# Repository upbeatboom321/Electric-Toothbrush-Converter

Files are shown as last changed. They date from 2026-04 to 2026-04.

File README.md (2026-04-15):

# Electric-Toothbrush-Converter

## Project Overview:

This project explores the design of a compact motor driven mechanism that converts a standard manual toothbrush into a high frequency electric toothbrush.

The goal is to design a mechanically efficient system that either: 1) produces strong, controlled vibration at the brush head or 2) a oscillating mechanism that moves that causes the brush to move with high frequency. All while remaining compact, handheld, battery powered, and modular.

## Problem Statement

Commercial electric toothbrushes are often expensive and proprietary. This project investigates whether a removable insert style handle can convert a standard manual toothbrush into a high frequency vibrating toothbrush using a compact DC motor system.

The challenge is efficiently transmitting vibration from the motor to the brush head without excessive damping or energy loss.

## Design Requirements

- Target vibration speed: 8000-20000RPM
- Power source: 3xAAA batteries in series
- Compact handheld form factor
- Replaceable manual toothbrush compatibility
- Safe and comfortable vibration amplitude

## Concept Selection

Two vibration approaches were considered.

Eccentric rotating mass motor/ vibration motor
A DC motor with an off center mass that generates vibration through centrifugal force.

Crank driven oscillation
A DC motor driving a crank mechanism that converts rotational motion into controlled angular oscillation.

Selected approach: The approach chosen for this project will involve a vibration motor. 

Rationale: A vibration motor was chosen over a crank driven oscillation mechanism because it is mechanically simpler, more compact, and easier to prototype. The vibration motor can generate high frequency motion with fewer moving parts, which reduces design complexity, manufacturing difficulty, and the risk of mechanical failure. This makes it more suitable for an early stage prototype where the main goal is to achieve noticeable brush vibration quickly and reliably.

## How the Mechanism Works

The vibration motor is mounted at the end of a link bar while the Toothbrush is clipped at the other end which allows to transfer vibration across.

## Mechanical Design

The mechanical system consists of:

- A Vibration motor
- A link bar
- A toothbrush clip
- A housing to support and align the mechanism

The mechanism is intended to be 3D printed for rapid prototyping and testing.

### Current Design Notes

- Motion type: Vibration motor
- Estimated motor vibration with brush: 8000-20000RPM
- Material: PLA plastic
- Mounting method: Press fit

---

## Electronics

### Planned Components

- Battery: 3xAAA batteries in series (4.5v)
- Switch: On off switch
- Motor control: direct power

### Electrical Goals

- Maintain stable motor speed under load
- Keep power system compact
- Avoid overheating
- Allow repeatable testing

---

## CAD and Prototyping

This project will use CAD and 3D printing to develop the mechanism and housing.

### Design Focus

- Lightweight moving parts
- Low backlash in the linkage
- Rigid motor mounting
- Compact toothbrush attachment system
- Easy disassembly for testing and iteration

---
# Current
---

## Current Specifications and Version

**Configuration:**  
- Motor: DC Coreless Vibration Motor 7x25mm, 1-6V Rated, 8000-20000RPM
- Power source: 3xAAA batteries in series
- Material: PLA plastic
- Brush attachment: Semi-cicrle like clip that goes around the lower midpoint of the brush

Current: Version 4
---

## Electrical Diagram

The electric wiring for this project is quite simple represented by the following diagram.

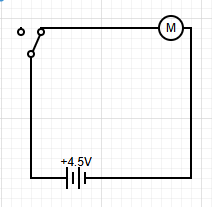
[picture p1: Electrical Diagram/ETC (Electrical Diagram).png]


Inside the acutal Main body of the ETC, where the battery positive and negative terminal make contact with the plastic, small pieced of metal were placed there connected to wires. This allows for the battery to be replacable while ensuring proper connection.

## Future corrections

The ETC is effective and there is substancial vibration at the brush head, however the vibration mechanism is making too much noise. The link bar making contact with the surrounding enviroment is causing the vibration to transfer to the whole body and not just the brush head. The vibration motor is further dampened by the switch located in side the main body due to it being to big and making direct contact with the motor. The case is okay but becomes uncomfortable to hold when brushing the top teeth. The brush also turns while brushing causing there to be less overall vibration.

Too make is product more effective: the material surrounding the link bar will need to make less contact while not degrading structual integrety, the switch will need to be smaller to give more room for the vibration motor, the casing will need to be more confortable to hold using ergonomic designs, the clip for the brush needs to be universal while firmly holding onto the any brush.

## Final Photos

![image alt]([https://github.com/upbeatboom321/Electric-Toothbrush-Converter/blob/edd6b2010d671f4ffcdd68ea69ed5afbbf082775/Electrical%20Diagram/ETC%20(Electrical%20Diagram).png](https://github.com/upbeatboom321/Electric-Toothbrush-Converter/blob/bc1a8993c03731aabfaebd6da449c6d216bca477/ETC%20Media/ETC%20(Final%20with%20everything).jpeg))

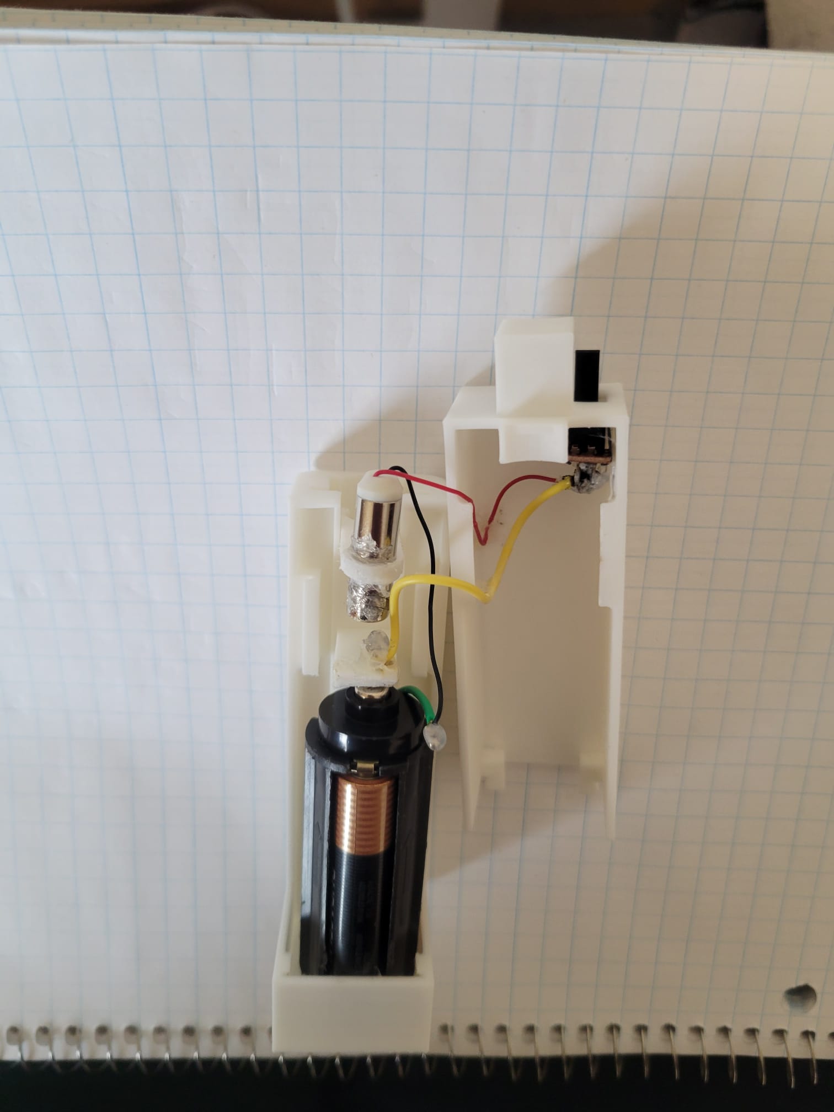
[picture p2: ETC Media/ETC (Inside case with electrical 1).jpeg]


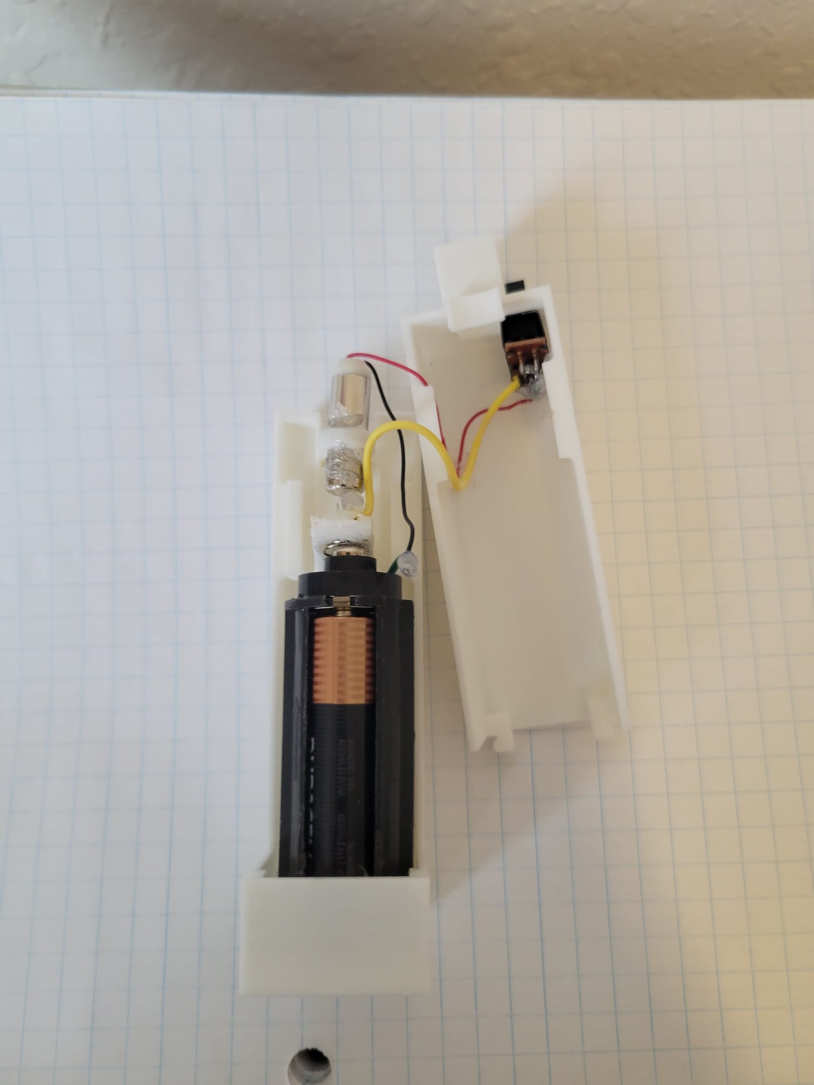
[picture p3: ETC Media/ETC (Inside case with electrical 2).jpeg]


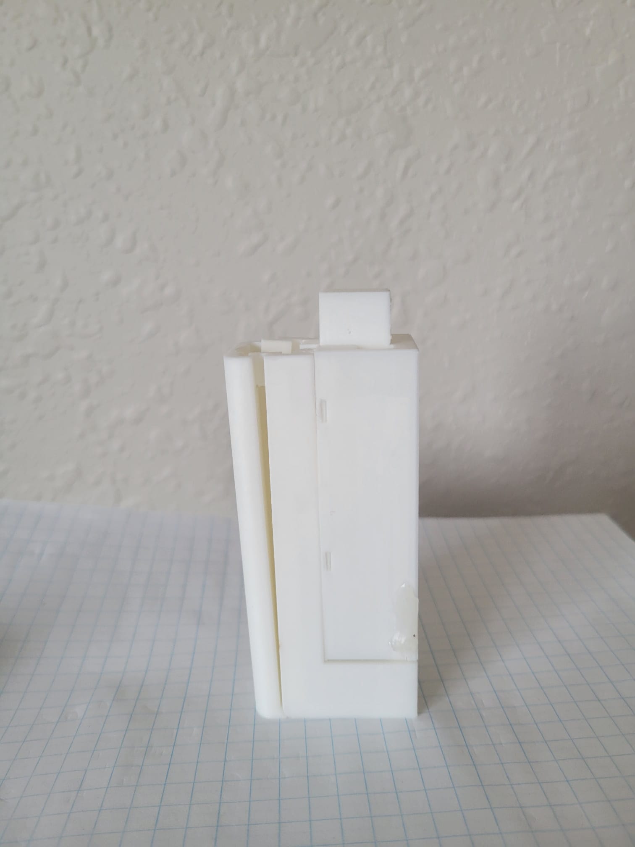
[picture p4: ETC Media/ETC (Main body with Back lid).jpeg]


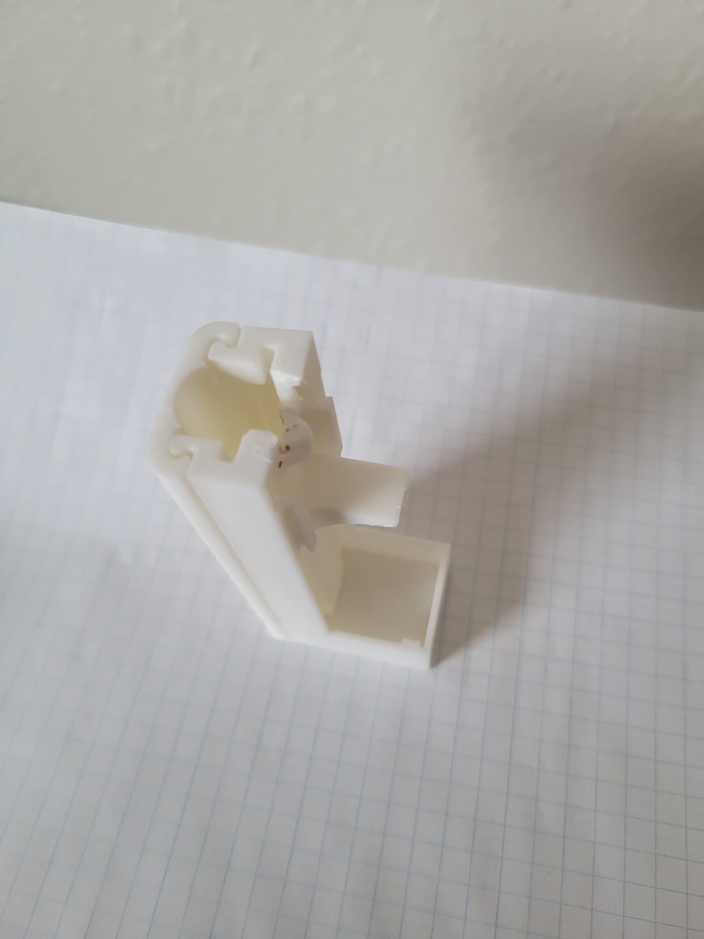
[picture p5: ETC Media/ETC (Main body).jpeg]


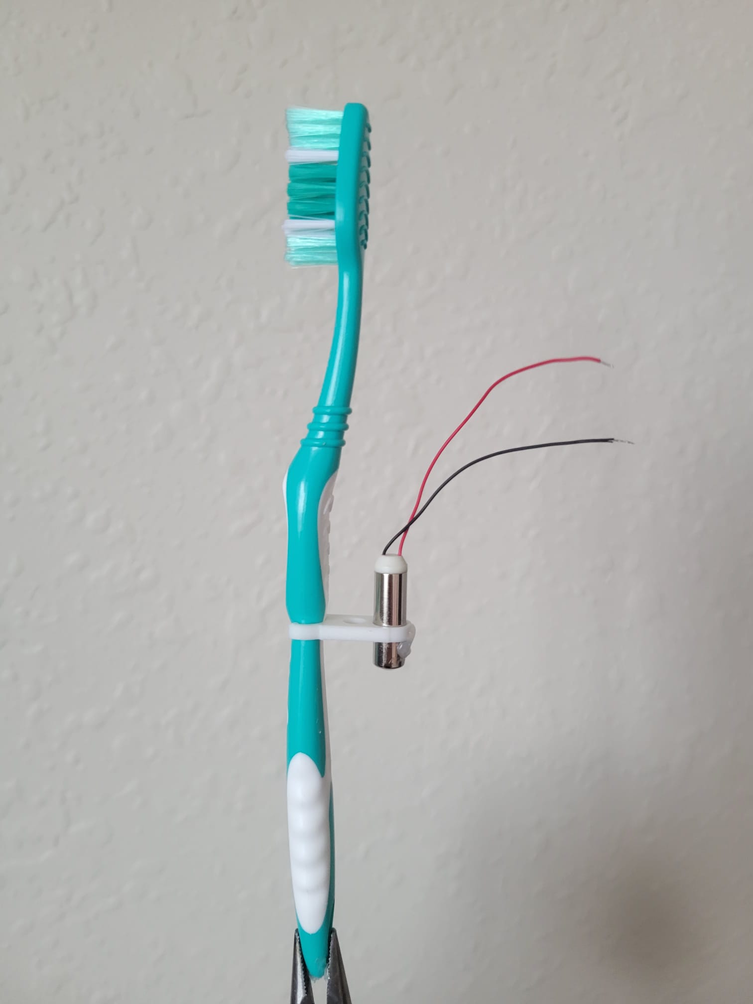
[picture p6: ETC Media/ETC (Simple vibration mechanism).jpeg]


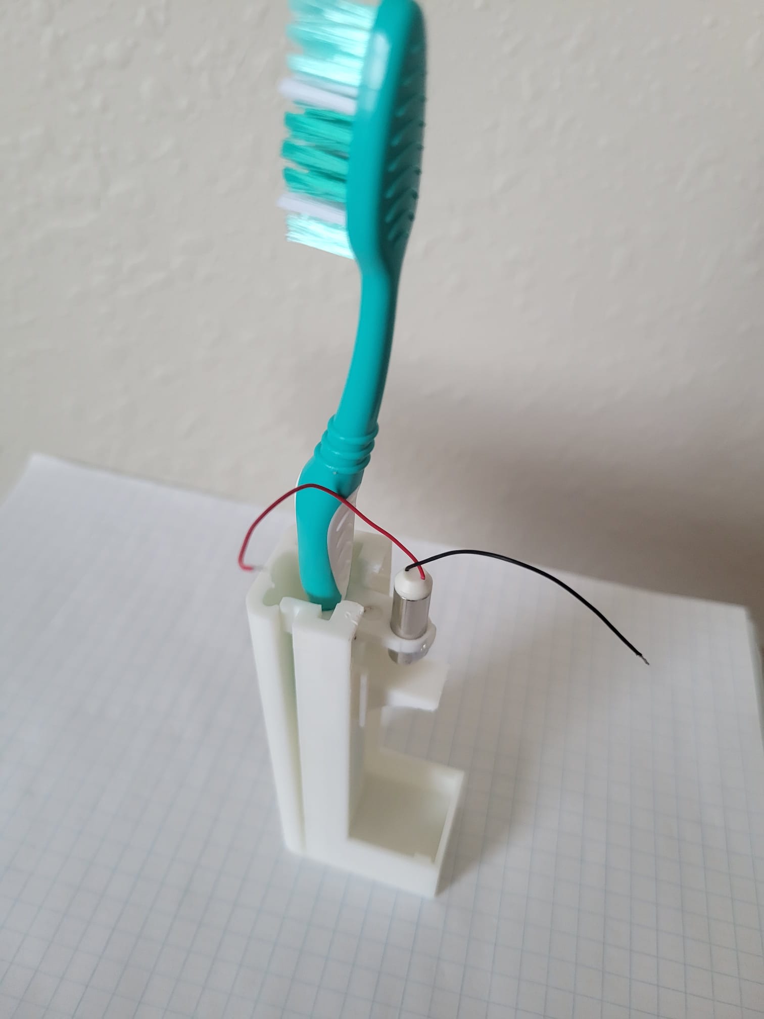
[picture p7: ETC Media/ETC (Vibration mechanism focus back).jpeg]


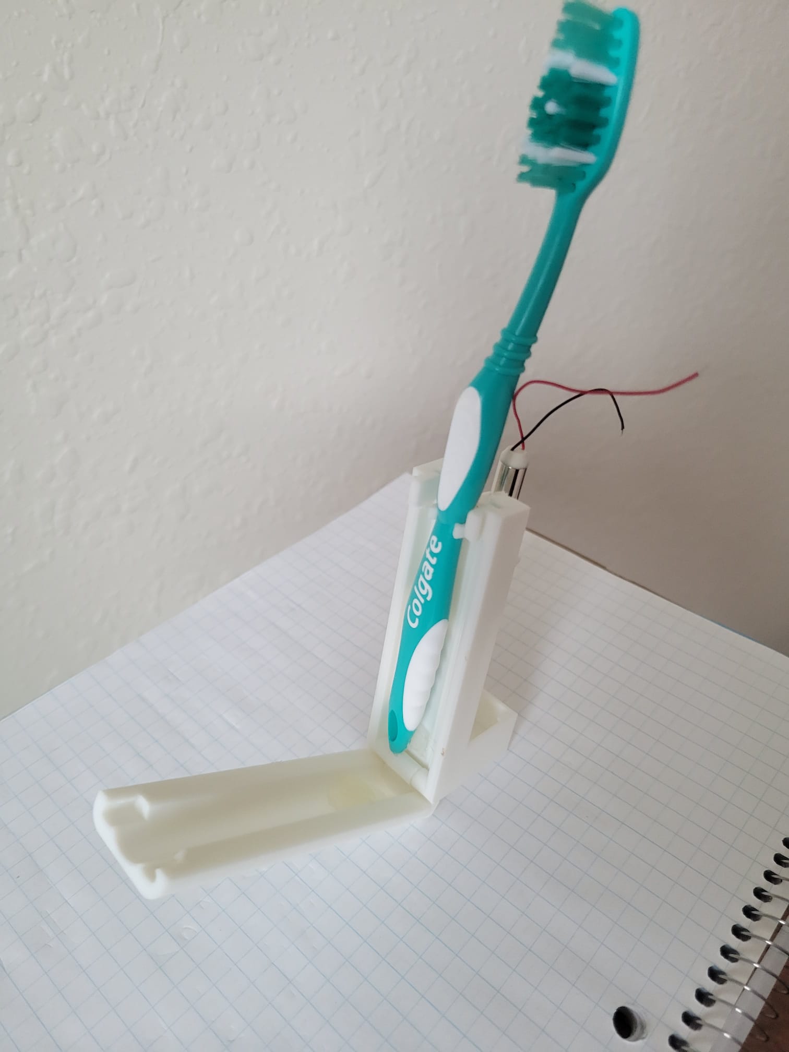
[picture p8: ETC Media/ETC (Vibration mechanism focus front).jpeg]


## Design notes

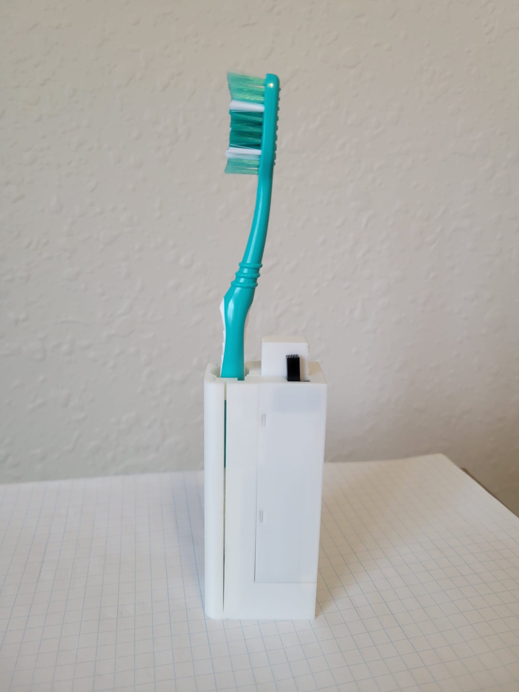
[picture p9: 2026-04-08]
ETC Media/ETC (Final with everything).jpeg

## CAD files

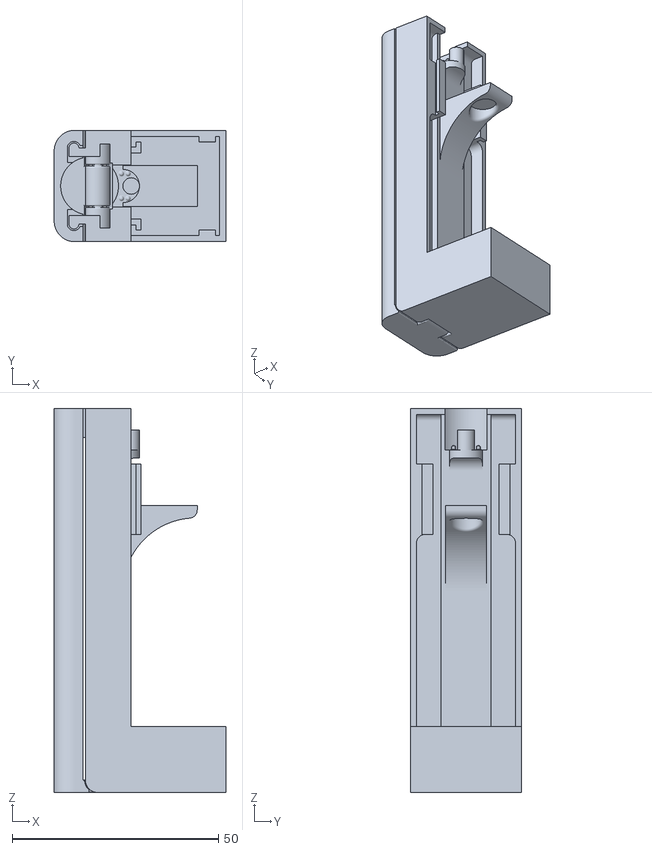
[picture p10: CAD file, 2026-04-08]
Version 4/ETC VIB CASE MAIN CASE (Version 4).stl
41.6 x 27.0 x 93.0

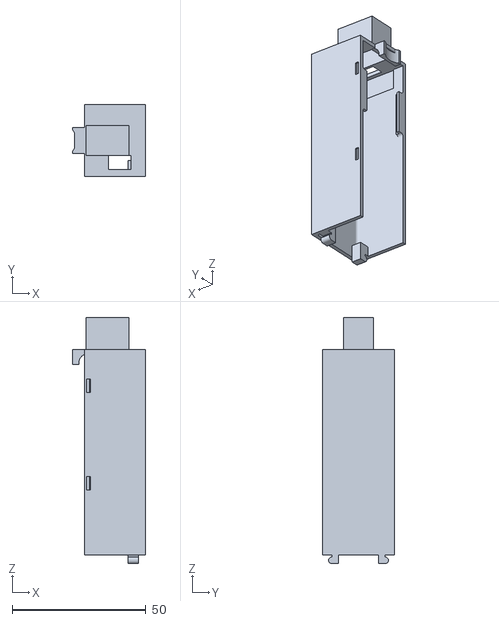
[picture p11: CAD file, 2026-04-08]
Version 4/ETC VIB CASE BACK LID (Version 4).stl
27.3 x 27.0 x 92.0

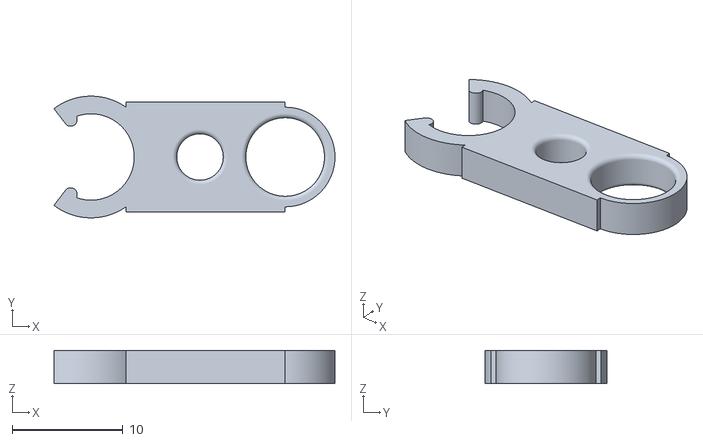
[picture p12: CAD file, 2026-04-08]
Version 4/ETC VIB LINK BAR (Version 4).stl
25.4 x 11.0 x 3.00

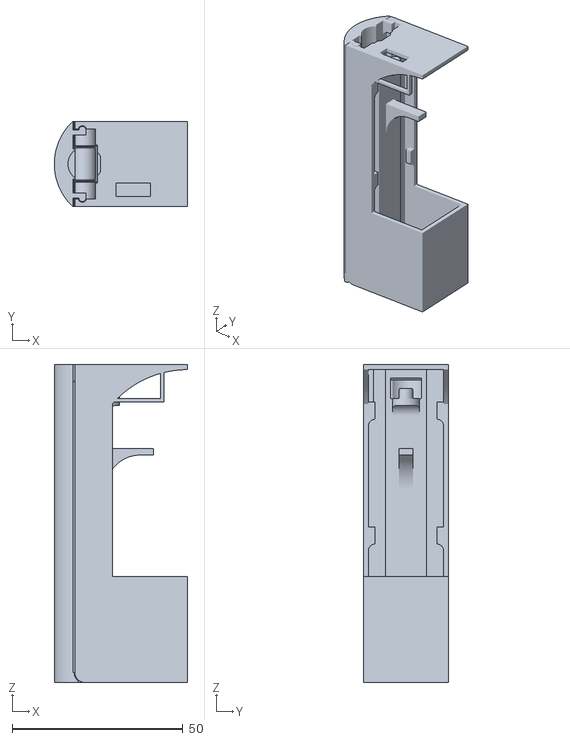
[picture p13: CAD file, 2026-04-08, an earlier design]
Version 1/ETC VIB CASE MAIN BODY (Version 1 ).stl
39.0 x 25.0 x 93.0

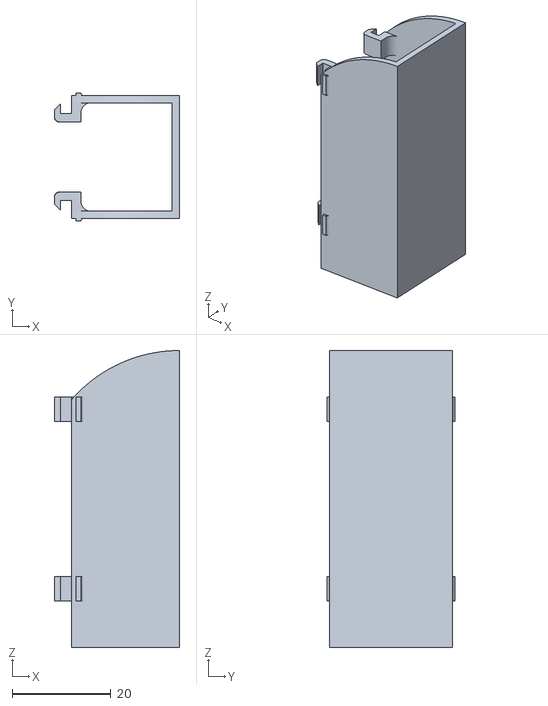
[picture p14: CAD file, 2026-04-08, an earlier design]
Version 1/ETC VIB CASE BACK LID (Version 1).stl
25.4 x 26.0 x 60.3

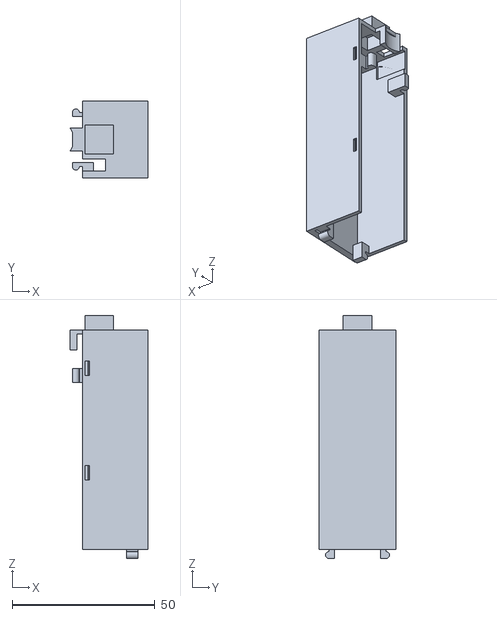
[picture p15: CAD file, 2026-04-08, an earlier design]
Version 2/ETC VIB CASE BACK LID (Version 2).stl
27.3 x 27.0 x 85.0

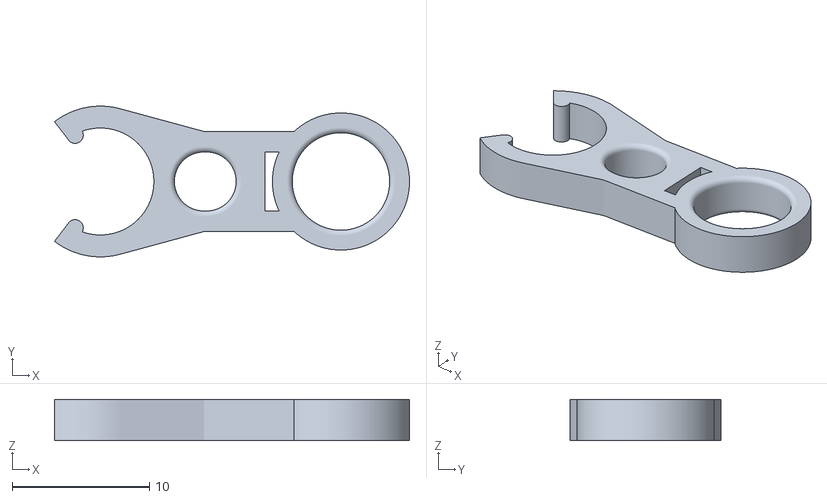
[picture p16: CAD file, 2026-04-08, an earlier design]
Version 1/ETC VIB LINK BAR (Version 1).stl
25.9 x 11.0 x 3.00

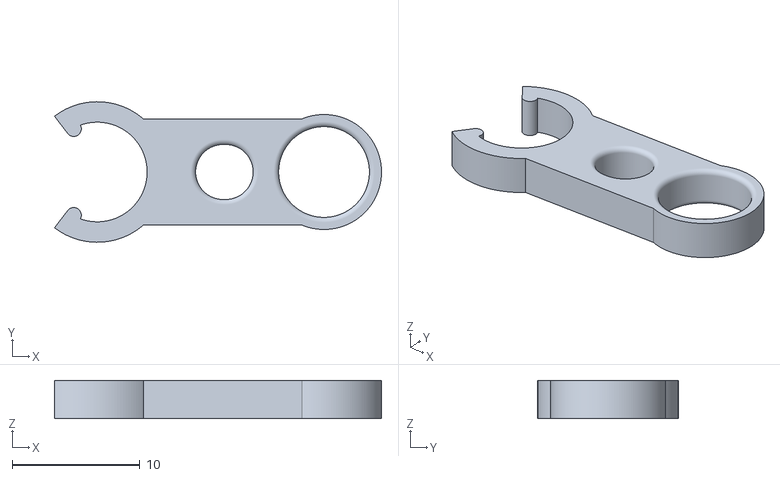
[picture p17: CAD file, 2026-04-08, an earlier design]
Version 2/ETC VIB LINK BAR (Version 2).stl
25.6 x 11.0 x 3.00

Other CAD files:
Version 2/ETC VIB CASE MAIN BODY (Version 2).stl
Version 3/ETC VIB CASE MAIN BODY (Version 3).stl
Version 3/ETC VIB CASE BACK LID (Version 3).stl
Version 3/ETC VIB LINK BAR (Version 3).stl

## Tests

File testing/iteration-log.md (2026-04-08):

# Iteration Log

## Initial Mechanism Test
**Date:** March 22 2026

**Build description:**  
Basic attempt to see the effectiveness of the vibration motor by attaching it to a link bar with the toothbrush at the other end

**Configuration:**  
- Motor: DC Coreless Vibration Motor 7x25mm, 1-6V Rated, 8000-20000RPM
- Power source: 5V
- Material: PLA plastic
- Brush attachment: Semi-cicrle like clip that goes around the midpoint of the bursh

**Test performed:**  
Motor and toothbrush were attached to the link bar with power was given to the motor to see how well the brush head will vibrate.

**Observations:**  
- The brush head was vibration quite well with this initial test with it being comparable to a cheap sonic toothbrush
- Vibration was transffered to the whole brush 

**Problems identified:**  
- Whole brush was vibrating meaning less energy is being transfferd to the brush head, however this is still effective as enough energy is transffered to the brush head. If issue needs to be addressed it will be done so during the case prototyping phase.

---

##  ETC Case Version 1
**Date:** March 28 2026

**Build description:**  
This case consists of 3 parts that are all individually printed. First we have the Main body where the toothbrush, battery, switch and vibration motor are to be installed in. The Main body has an opening hatch using a hinge to open and insert you toothbrush. Second we have the Back lid which will allow easy access to the batteries, switch and motor. Lastly we have the link bar which will attach to the toothbrush and will be mounted inside the Main body. This is a very simple design only to accomade the minimum requirements to make this project succeed.

**Configuration:**  
- Motor: DC Coreless Vibration Motor 7x25mm, 1-6V Rated, 8000-20000RPM
- Power source: 3xAAA batteries in series
- Material: PLA plastic
- Brush attachment: Semi-cicrle like clip that goes around the lower midpoint of the bursh

**Test performed:**  
All pieces were put together to see if all parts and components fit as intended.

**Observations:**  
- Back lid is not able to firmly attch to the body and contact point have broken off due to being to thin
- Nearing the top of the Main body, the 3d printer has difficulty printing the top portion without any supports
- The mechanical switch and link bar locations are too close together casing interference
- The link bar is not able to get into it's positon because of tight fitting
- Battery postive contact point keeps slipping from it's intended postion
- Opening hatch for brush is too dificult to open and close
- Difficulty putting the battery in

**Problems identified:**  
- Back lid contact points need to be changed for more clearance and strength
- A support structure will be designed for easy printing of top portion on Main body
- The whole case will need to be bigger to accomadate these changes so no part will interfere with each other
- Battery postive contact point will need to be widened
- Opening hatch will be redesigned to require less effort
- The hole for the brush it too tight
- There is too much material in the back causing the battery not to fit

---

## Version 2
**Date:** March 30 2026

**Changes from Version 1 with reasoning:**  
- Back lid contact point design changed: becuase previous design was weak and broke eaisily
- Overall case size increased: to make room for components inside
- Back lid overall design change: Due to reoccuring issues with a suitable design to put the link bar into place and easier access to back components
- Battery postive contact point widened: for more consistent contact betweeen the two
- Opening hatch redesigned: to require less effort to open
- Brush hole widened: because brush it too tight
- Material removed from Back lid: so battery can fit

**Build description:**  
This case consists of 3 parts that are all individually printed. First we have the Main body where the toothbrush, battery, switch and vibration motor are to be installed in. The Main body has an opening hatch using a hinge to open and insert you toothbrush. Second we have the Back lid which will allow easy access to the batteries, switch and motor. Lastly we have the link bar which will attach to the toothbrush and will be mounted inside the Main body. This is a very simple design only to accomade the minimum requirements to make this project succeed.

**Configuration:**  
- Motor: DC Coreless Vibration Motor 7x25mm, 1-6V Rated, 8000-20000RPM
- Power source: 3xAAA batteries in series
- Material: PLA plastic
- Brush attachment: Semi-cicrle like clip that goes around the lower midpoint of the bursh

**Test performed:**  
All pieces were put together to see if all parts and components fit as intended.

**Observations:**  
- Back lid contact points broke again
- Opening hatch clipping mechanism was too dificult to open
- Link bar fitting was too tight
- Battery positve contact point difficult to pull out

**Problems identified:**  
- Back lid contact points do not have enought clearance and strength
- More cleance for opening hatch clipping mechanism
- Link bar location too tight
- Battery positive contact point it too rough

---

## Version 3
**Date:** April 4 2026

**Changes from Version 2:**  
- Thickened Back lid: to make it stronger
- Gave more room for the opeing hatch mechanism: so there is less of a struggle to open it after printing it
- Made more space for the link bar: for it to fit
- Added a fillet to the battery positive contact point: to make it eaiser to remove becuase there was difficulty before

**Build description:**  
This case consists of 3 parts that are all individually printed. First we have the Main body where the toothbrush, battery, switch and vibration motor are to be installed in. The Main body has an opening hatch using a hinge to open and insert you toothbrush. Second we have the Back lid which will allow easy access to the batteries, switch and motor. Lastly we have the link bar which will attach to the toothbrush and will be mounted inside the Main body. This is a very simple design only to accomade the minimum requirements to make this project succeed.

**Configuration:**  
- Motor: DC Coreless Vibration Motor 7x25mm, 1-6V Rated, 8000-20000RPM
- Power source: 3xAAA batteries in series
- Material: PLA plastic
- Brush attachment: Semi-cicrle like clip that goes around the lower midpoint of the bursh

**Test performed:**  
All pieces were put together to see if all parts and components fit as intended. The motor is then turned on to see how well the vibration is transffered throught the link bar into the brush.

**Observations:**  
- Counld not fit the link bar into position
- The Main body was vibrating quite a bit

**Problems identified:**  
- There was room for the link bar in its desired postiion but I couldn't get it into their becuase the surrounding area was tight
- Too much surface contact between the link bar and main body

- ---

## Test 4
**Date:** April 6 2026

**Changes from Version 3:**  
- Side areas around the link bar were shortened: so that the link bar can fit
- Small pillars were added were the link bar made contact with the main body: to reduce overall surface friction

**Build description:**  
This case consists of 3 parts that are all individually printed. First we have the Main body where the toothbrush, battery, switch and vibration motor are to be installed in. The Main body has an opening hatch using a hinge to open and insert you toothbrush. Second we have the Back lid which will allow easy access to the batteries, switch and motor. Lastly we have the link bar which will attach to the toothbrush and will be mounted inside the Main body. This is a very simple design only to accomade the minimum requirements to make this project succeed.

**Configuration:**  
- Motor: DC Coreless Vibration Motor 7x25mm, 1-6V Rated, 8000-20000RPM
- Power source: 3xAAA batteries in series
- Material: PLA plastic
- Brush attachment: Semi-cicrle like clip that goes around the lower midpoint of the bursh

**Test performed:**  
All pieces were put together to see if all parts and components fit as intended. The motor is then turned on to see how well the vibration is transffered throught the link bar into the brush.

**Observations:**  
- Everything fit well in their desired positions.
---
